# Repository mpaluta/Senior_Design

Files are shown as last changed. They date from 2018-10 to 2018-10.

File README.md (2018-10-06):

# Senior_Design

This repo hosts materials related to the design of "Flappy Bird", an endearingly-named RC airplane for our Notre Dame aerospace engineering senior design class. We designed, fabricated, and tested our airplane to perform to prescribed mission requirements.  

Our final report is located [here](/Box%20Files/Final%20Report/Final%20Report.pdf).

Takeoff and flight demo is located [here](Images/Takeoff_and_Flight.mov)

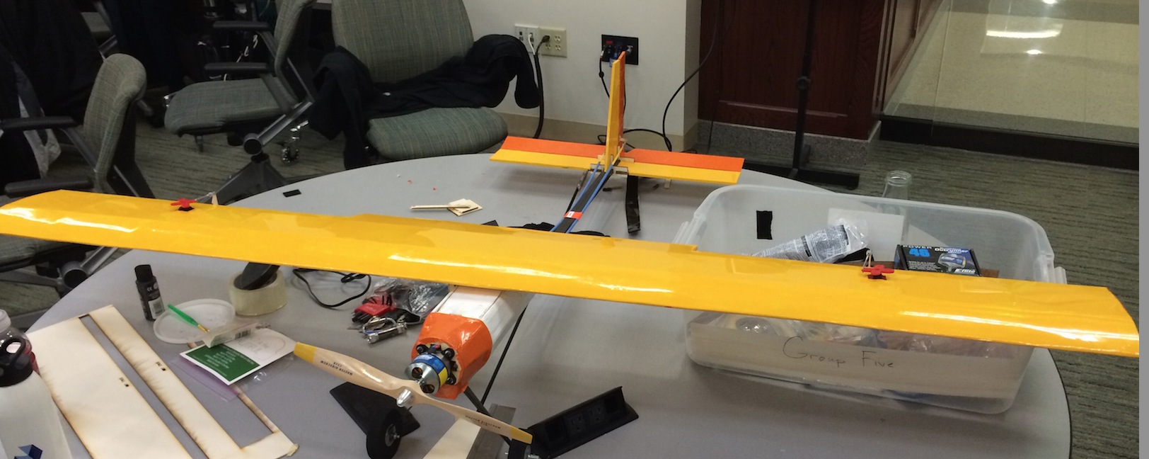
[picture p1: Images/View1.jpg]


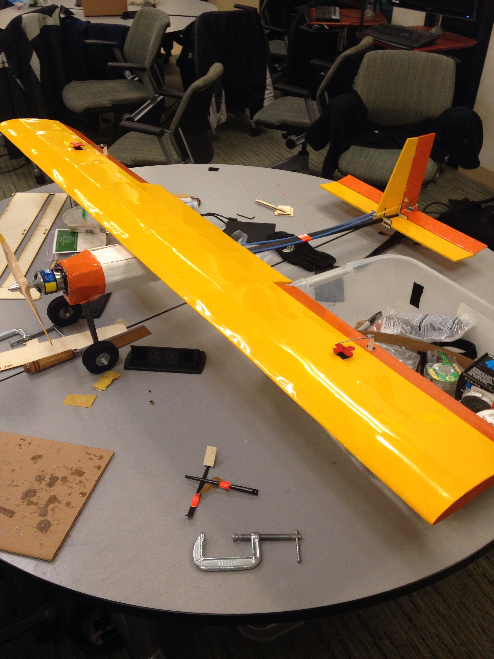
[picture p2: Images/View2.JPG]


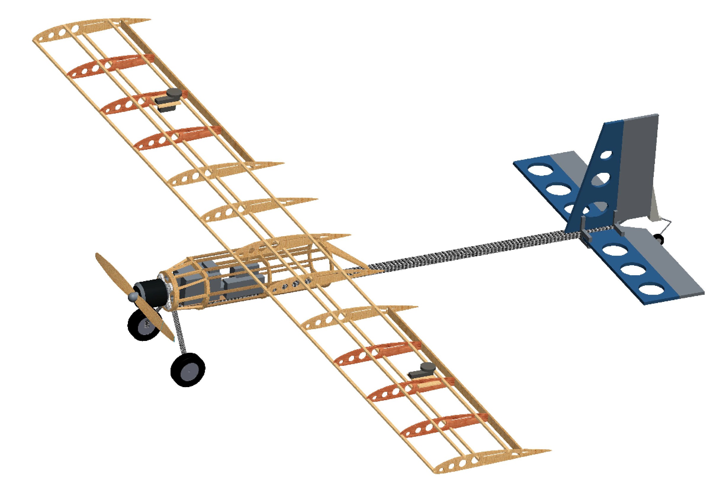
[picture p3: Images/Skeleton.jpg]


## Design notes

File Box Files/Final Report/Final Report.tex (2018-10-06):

\documentclass[titlepage]{article}
\usepackage{graphicx}
\usepackage{indentfirst}
\usepackage{array}
\usepackage{gensymb}
\usepackage{pdfpages}
\usepackage[bottom]{footmisc}
\usepackage[title,titletoc,toc]{appendix}
\renewcommand{\thetable}{\Roman{table}}
\renewcommand{\baselinestretch}{1.35}
\usepackage[margin=1in]{geometry}
\setlength{\parindent}{.4in}

\usepackage{fancyhdr} 
\pagestyle{fancy}
\lhead{\textsf{Design and Flight Analysis of the Remote-Controlled Flappy Bird Aircraft}}
\rhead{\textsf{\thepage}}
\cfoot{}
\renewcommand{\headrulewidth}{0.4pt}
\renewcommand{\footrulewidth}{0.4pt}

\begin{document}
\title{\textbf{Design and Flight Analysis of the Remote-Controlled Flappy Bird Aircraft}}
\author{Brian Quinn, Mark Paluta, Eliseo Miranda, Patrick Wall}
\date{May 9, 2014}
\maketitle

\begin{abstract}
Scale model, remotely-controlled aircraft are used extensively for hobby pilots, but also serve a secondary, educative purpose of allowing university students to apply aerodynamic theory to a physical flight application. In this design project, a high aspect ratio, low wing loading aircraft was designed to fly a mission in which it would be required to fly to high altitudes before performing an unpowered descent back to its cruising altitude. Implementing performance characteristics calculated using principles of fluid mechanics and aerodynamics, along with historical data from previous designs, the team of student engineers designed a minimalist vehicle, constructed from light woods and carbon fiber, that demonstrated speeds of up to 48 mph with climb rates as high as 1246 ft/min to meet the mission requirements, surpassing pre-flight predictions. Although flight data indicates that glide predictions far exceeded the observed values, the plane was able to successfully progress through each phase of the mission profile without issue and proved to be both maneuverable and well-controlled in the air, leaving the designers with confidence that subsequent design iterations would allow those performance issues to be resolved.
\end{abstract}

\tableofcontents
\addcontentsline{toc}{section}{List of Figures}
\addcontentsline{toc}{section}{List of Tables}
\listoffigures
\listoftables
\pagebreak

\section{Introduction}
For years, remotely-controlled aircraft have captured the interests of hobby enthusiasts of all ages and skillsets, combining ease of operation with a multitude of designs available as kits, templates, or ready-made models. For students at the university level, however, who have had exposure to flight principles like aerodynamics, dynamics, and fluid mechanics, scale aircraft provide a unique opportunity to translate that theory into a physical application at relatively low costs, allowing students to explore untested design concepts and construction ideas in an environment that celebrates challenges and mishaps as an opportunity to learn. 

It is this concept that inspired the 2014 senior design capstone project for which students were tasked with working cohesively as a team to construct viable aircraft, complete with useable control surfaces, guided by their knowledge of aerodynamics concept and the skills of seasoned pilots. Steered by a mission mandate requiring that each aircraft be designed to climb to as high an altitude as possible in ten seconds before performing an unpowered glide back down to the cruising altitude, the four students of DBC Industries, referred to herein as the Team, created an aircraft colloquially referred to as, ``The Flappy Bird", a minimalist airframe designed to climb quickly while also allowing the craft to glide for long periods of time. This report details the design and construction process of the final vehicle and also analyzes the results of preliminary flight testing, permitting a comparison of predicted vehicle maneuverability and the observed capabilities during flight.

\section{Mission Profile}
The mission profile for this design project, as alluded to previously, consists of three distinct phases of flight operation. In Phase I, the aircraft must take off under its own power and maintain low altitude, level flight while its stability and control are verified by the remote pilot. Pending a successful checkout, the aircraft then proceeds to Phase II in which it must begin to climb to as high an altitude as possible in a ten second interval. From there, Phase III begins with a short period of high altitude, level flight before the craft returns to its original altitude through an unpowered glide, with focus placed on the rate of descent of the aircraft. 

\section{Detailed Design}
\label{design}
Before construction began on the physical aircraft, an exhaustive design process was undertaken to ensure the mission requirements could be met during flight testing, guided by the designation of two primary design drivers. Of utmost concern was the aircraft's overall weight. Although the aircraft was required to carry data collection sensors and servo motors to drive the control surface deflections, the Team chose a minimalist approach to the design of the fixed structure. Unlike service aircraft which require a rigid, metal skin around the fuselage and wing surfaces, the conditions under which these scale aircraft flew exacted far less stress on the airframe, allowing large portions of the structure, that might otherwise be covered in wood sheeting, to be replaced with monokote, a plastic covering that bonds to materials when heated. As the CAD model in Figure \ref{noskin} shows, the elimination of rigid skin allowed the Team to use wood only where necessary to defined the shape of the airframe or to provide a surface onto which sensors and other payloads could rest.
\begin{figure}[h]

\caption{Isometric view of CAD model highlighting minimalist airframe structure}
\label{noskin}
\end{figure}
These material savings along with use of light woods such as balsa and spruce allowed the Team to construct a robust aircraft with a low structure weight, putting less stress on the motor during climb and requiring less of the wing during the descent glide.

To further address the issue of weight, a rectangular carbon fiber rod was chosen as the main structural element of the fuselage. As the backbone for both the fuselage and tail assemblies, the rod would take most of the stress on the airframe during flight, but would do so with minimal added weight. The fuselage was approximately cylindrical, tapering off in roughly a cone at the trailing edge and built up from the carbon fiber rod that ran through the length of its underbelly. It also housed most of the internal electronics with the exception of two aileron servos and a pitot tube in the main wing. Protruding from the front of the fuselage structure was a double-thick bulkhead upon which the motor and propeller assembly were affixed.

Located under the fuselage and epoxied directly to the front end of the carbon fiber rod, the main landing gear, experienced the most stress of any component on the aircraft due to its direct impact with the ground on landing attempts, and thus was attached strongest part of the aircraft allowing the gear system to transfer energy out of its legs upon impact. The connection points to the fuselage were also reinforced with a plywoord box, epoxied to the carbon fiber on both sides of the gear, to prevent any torquing motions from ripping the gear off of the aircraft. At the aft end of the aircraft, a small, steerable wheel was attached directly to the rudder, reducing the number of mechanical linkages and improving the takeoff performance due to the increase angle of attack of the wing while rolling on the ground. Attaching the wheel to the rudder negligibly reduced the ground control of the aircraft but improved weight characteristics, which was more desirable for the given mission profile.

The secondary driver employed in this design was a high lift-to-drag performance ratio. As outlined in the course textbook, a high lift force with a correspondingly low drag force promotes a lower descent rate during the gliding phase of flight, allowing the aircraft to remain aloft for proportionally longer periods of time. Although drag is a phenomena affecting all parts of the aircraft structure, the design of the main wing was of greatest concern to the Team as it has the largest overall effect on the ratio and, consequently, was the most challenging and, arguably, most important aspect of the design. 

Climb and glide are located at the opposite ends of the design spectrum when seeking an optimimum aspect ratio for a main wing. A small aspect ratio will help with climb and maneuverability while a large aspect ratio increases the performance during glide. To address each of these, an aspect ratio of 7 was selected to strike a mean between the two extremes, leading to a total wing span of 66 inches and a constant chord length of 9.6 inches. These design characteristics were implemented using a Clark Y flat-bottom airfoil. Used extensively in remote-controlled aircraft applications, the flat bottom afforeded the Team the ability to attach a mounting plate to the underside of the wing, allowing it to rigidly screw down onto the fuselage structure. The Clark Y also has the advantage of excellent lifting qualities at the low to middle range angles of attack at which the aircraft would be flying. A detailed drawing depicting the Clark Y shape and the rib structure of the aircraft can be found below in Figure \ref{wing} which also highlights the dimensions of the main wing structure.

\begin{figure}[h]
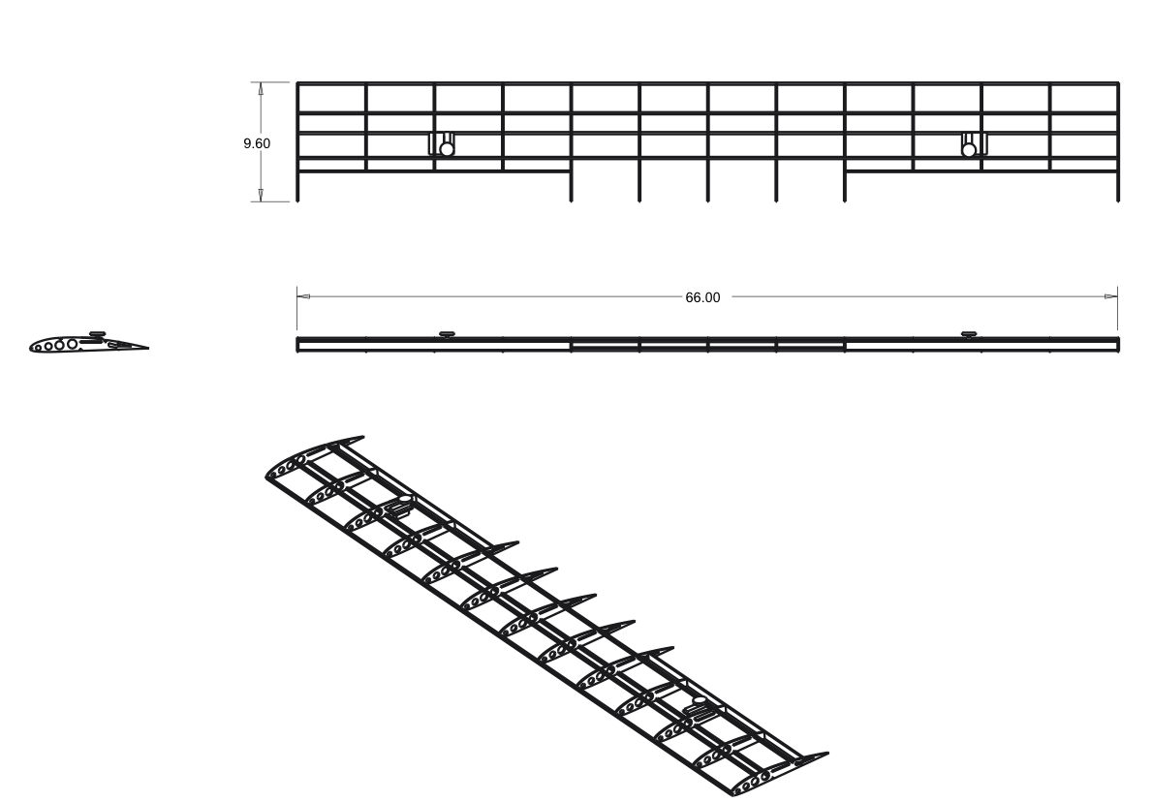
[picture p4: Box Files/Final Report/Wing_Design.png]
 
 \caption{Dimensioned model of the main wing depicting rib structure as well as airfoil shape and positioning.}
\label{wing}
\end{figure}

The tail was of conventional design placed at the free end of the carbon fiber rod protruding from the fuselage as seen in Figure \ref{noskin}. One of the main concerns of this design, however, was the potential for severe torquing from the lift forces generated by the tail surfaces. Addressing these issues early in the design process, the thickness of the carbon fiber rod was doubled, as was the thickness of the plywood used to construct the tail surfaces, leading to structurally sound design as seen in Figure \ref{tail} below, which also highlights the main dimensions, in inches, of the horizontal and vertical tail surfaces. A custom bracket was designed for the attachment of the tail surfaces to the carbon fiber, and each tail surface was anchored, using epoxy, to the bracket at two locations, thus preventing twisting. The elevator and rudder control surfaces were overdesigned to provide more than sufficient control of the aircraft and prevent flutter or twist in-flight. Although Figure \ref{tail} shows large holes in the tail surface, these were monokoted over in the final design, allowing weight savings without any detriment to performance.

\begin{figure}[h]
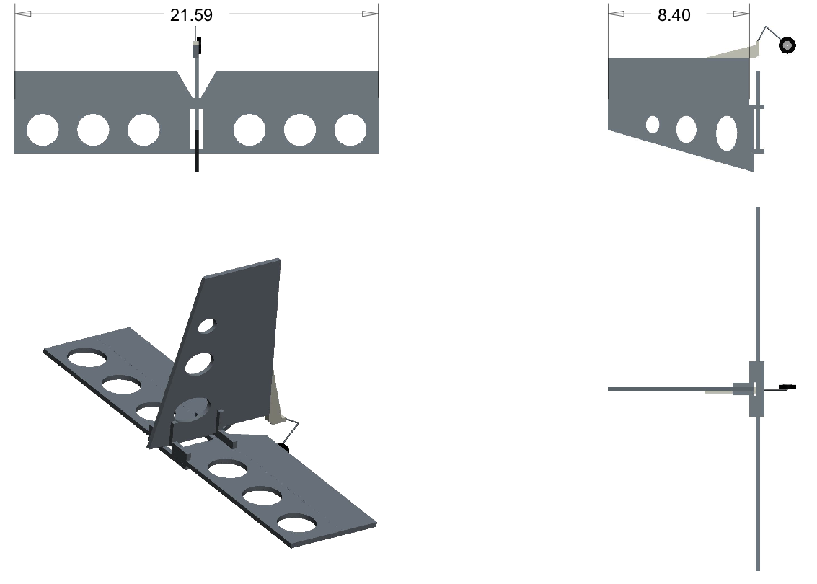
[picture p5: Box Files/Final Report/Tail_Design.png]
 
 \caption{Tail design detailing important dimensions and weight-saving structural designs.}
\label{tail}
\end{figure}
 
Rouding out the design, the aircraft used a 1.25 horsepower motor, capable of providing approximately 3.5 pounds-force of thrust. With a final takeoff weight of 5 pounds, including a 0.84 pound payload, this yielded a final thrust-to-weight ratio of 0.7. The motor powered a 13-inch propeller with an 8-inch pitch which created the power to move the craft through the air. As the main wing was bolted onto the fuselage before flight, hatches in both the top and side of the fuselage were used to allow access to internal components without removing the wing. The final flight vehicle is shown below in Figure \ref{real} in a picture taken just seconds after the final component of the fuselage was added, completing the craft.

Design characteristics of the aircraft were chosen using a Figure of Merit analysis, detailed and tabularized in Appendix A. The Figure of Merit analysis assigns numerical weights to different component designs based on drivers such as weight and size. The component with the most favorable weighting and ease of construction was the one chosen for use in the design.
\begin{figure}[h]
 
 \caption{Flappy Bird aircraft seconds after completion}
\label{real}
\end{figure}

\section{Predictions from Spreadsheet Analysis}
As part of the detailed design, a series of spreadsheets were used to determine relative values for vehicle handling qualities and component design. Perhaps one of the most integral factors for determining the aircraft's ability to perform well within the mission constraints is the wing loading as it plays a significant role in both an aircraft's climb and glide performance. As mentioned previously, glide performance is the mission phase in most need of optimization and, as such, the wing loading on the vehicle was determined based on performance during descent, for which a low wing loading is desired. Assuming a ground elevation of 823 feet in Bremen, Indiana, the town in which the field is located, the wing loading during glide was predicted to amount to approximately 13 oz/ft$^2$, a value corroborated by the pilots who would be controlling the aircraft during flight testing.

Given these flight characteristics and data culled from previous years' planes, the final climb rate of the aircraft was predicted to be 1,100 feet per minute, although the Team determined early on that the actual rate would decrease due to the structure weight of the high aspect ratio wing. Over the stated ten second time interval, this climb rate predicted a gain in altitude of approximately 200 feet. Assuming the unpowered glide would begin at this altitude, it was estimated that the aircraft would lose 152 feet of altitude every minute, thus requiring approximately 78 seconds to return to its original cruising altitude. As before, this glide rate assumes ideal flight conditions and is expected to diminish somewhat during flight testing. While at level flight, the design parameters in the spreadsheet predicted a cruising speed of 44 miles per hour.

Those spreadsheets that were used in the design process are attached at the back of this report as Appendix B. It should be noted that these were used merely as guides for ranges of acceptable values and, in many cases, actual design decisions were made based on input from both the pilots and teaching assistants who pulled design advice from previous experience.

\section{Flight Test Results}
During flight testing, the Flappy Bird flew a total of two test runs, each following the three phases of the mission profile. To numerically track the performance of the aircraft on these flights, altitude and speed data were collected by an onboard sensor package, including a pitot static tube mounted starboard wing tip. After eliminating the data collected while the plane was readied for flight, Figure \ref{Trial}, containing altitude data over each test flight, and Figure \ref{speed}, a graphic showing the speed of the aircraft during its flight testing, were produced to give a reader a visual representation of the information collected during flight testing.

\begin{figure}[h]
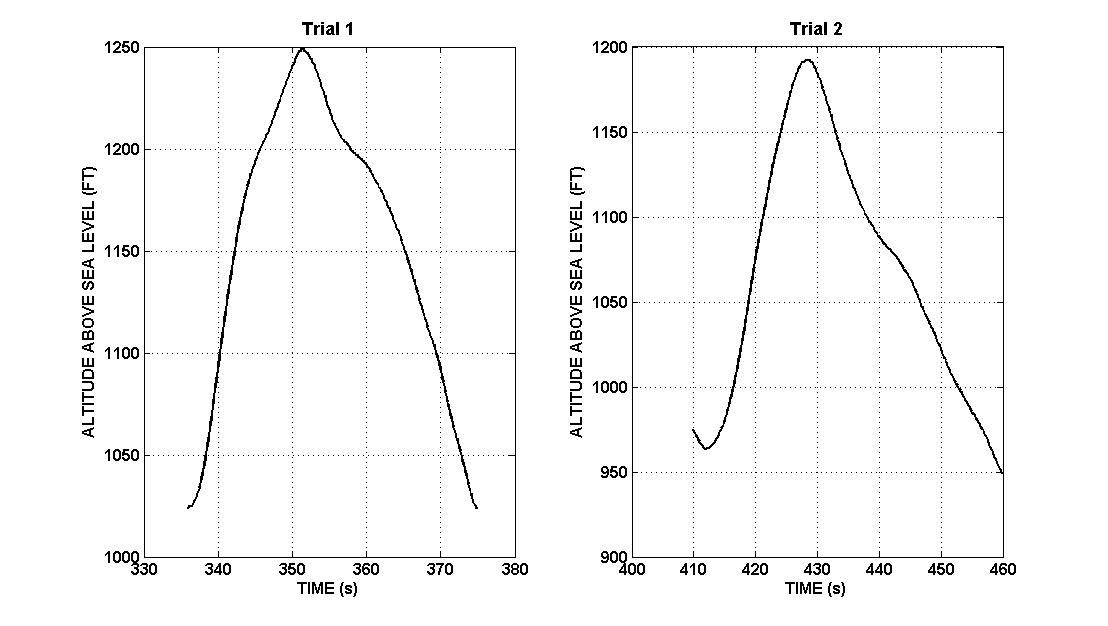
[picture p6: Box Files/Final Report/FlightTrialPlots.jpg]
 
 \caption{Climb and descent profiles flown by the Flappy Bird aircraft during two flight tests.}
\label{Trial}
\end{figure}

\begin{figure}[h]
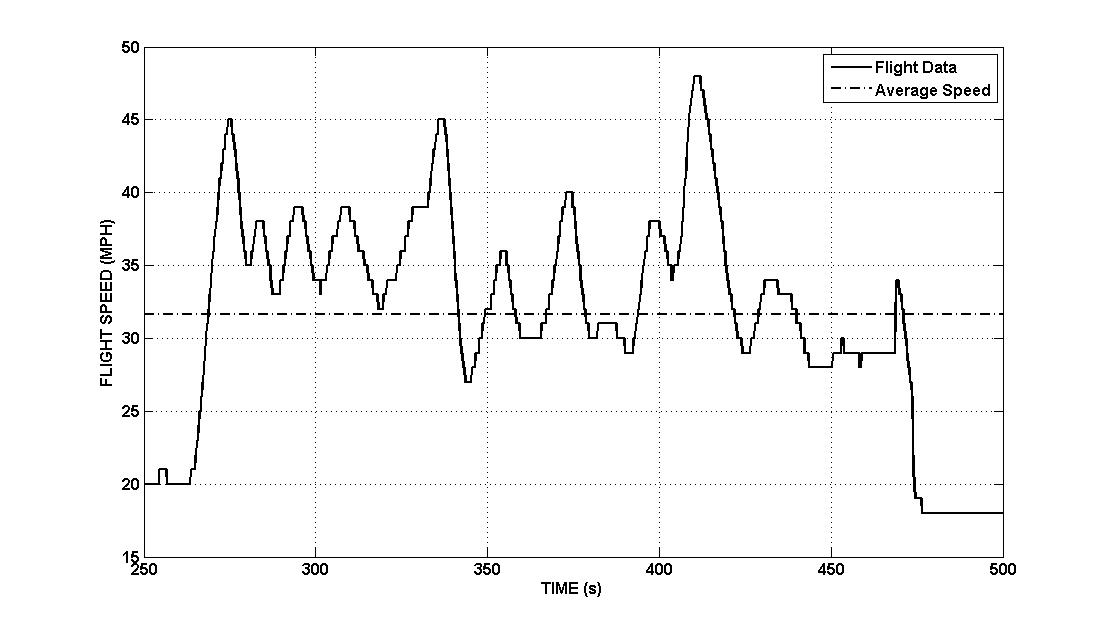
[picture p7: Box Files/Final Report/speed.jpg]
 
 \caption{Speed of Flappy Bird aircraft measured by onboard sensors throughout flight test.}
\label{speed}
\end{figure}

Focusing first on Figure \ref{Trial}, one can easily see that the climb and glide performance were similar through both test flights. In Trial 1, the aircraft was able to make a rapid ascent to an altitude of 1250 feet above sea level, or approximately 400 feet above the ground before gliding back to its original cruising altitude in a time interval of 24 seconds. In Trial 2, the pilots were able to make a more uniform climb up to the aircraft's peak altitude of 1900 feet above sea level before gliding back down to altitude in 26 seconds. 

Using this data, the Team was able to calculate rates for both ascent and descent for the two flight profiles. The maximum rate of climb for this aircraft, 1246 ft/min occured in the first leg of the ascent in Trial 1 as illustrated by the steep gradient from the cruising altitude to approximately 1200 ft. That ascent also saw the lowest rate of climb, 548 ft/min, during the final climb from 1200 feet to 1250 feet in altitude.

In a similar manner, the Team also conducted an analysis of descent, or glide, rates. As depicted clearly in the Trial 2 diagram of Figure \ref{Trial}, the final leg of descent, from approximately 1050 ft to the cruising altitude, represents the slowest measured rate of descent of the aircraft at 405 ft/minute. This was counteracted by a 596 ft/min descent rate between 1200 ft and the cruising altitude in Trial 1.

Each of the two trials depicted in Figure \ref{Trial} took place during a single, continuous test flight. Therefore, Figure \ref{speed}, upon which focus will now be placed, depicts the aircraft speed through both trials from first takeoff to final landing. As the horizontal dashed line indicates, the mean speed of the aircraft during its test flights was 31.6 mph, a number clearly affected by the low-speed regions of the figure surrounding takeoff and landing. During the flight, however, the aircraft also reached a peak speed of 48 mph, showing that speeds like the 44 mph predicted by the spreadsheet were, in fact, possible with this aircraft.  

Using this flight data the figure of merit for the flight testing, the success factor, was calculated using the formula presented in Equation \ref{success} as

\begin{equation}
S = (dH/dt)_c + (dH/dt)_g - \Delta(dH/dt)_c - \Delta(dH/dt)_g,
\label{success}
\end{equation} 
where $(dH/dt)$ represents the rate of climb or glide, identified by the subscripts ``c" and ``g", respectively, and $\Delta(dH/dt)$ represents the absolute difference between the predicted and actual rates of climb and glide following the same subscript identifications as before. After calculating each of these quantities, the flight success factor was determined to be 441.94 ft/min, approximately 47 \% of the success factor of 947.66 ft/min calculated assuming a perfect ascent and descent using the numbers produced by the design spreadsheets.

\section{Discussion}
For a first iteration of a design idea, the Flappy Bird performed admirably during its flight testing and proved an airworthy and highly maneuverable aircraft. As the success factor indicates, however, further iterations would require that work be done to improve its performance in a few key areas. As mentioned in Section \ref{design}, the two primary design drivers were geared towards optimizing the glide rate of the aircraft, an area in which the aircraft, admittedly, struggled. Its performance in this area, however, is well explained.

On the day of flight testing, strong winds were predicted and observed at the field during most of the flight test runs, this test proving no exception. Although these winds were within the acceptable limits of flying, they did have a deleterious effect on the rates of climb and glide due to their negative effects on the lifting surfaces. During ascent to the peak altitude, the pilots chose to climb at an angle of attack lower than might have normally been pursued to prevent the wind from causing a nose up moment that might stall the wing. Therefore, the rates shown in Figure \ref{Trial} may not necessarily be representative of the full capabilities of the aircraft. Similarly for glide, although the pilots attempted to fly into the wind to gain favorable lift performance, strong updrafts continued to push the wing towards stall, necessitating that they enter onto a steeper glide slope than might otherwise have been possible. The pilots, however, push the plane to the best acceptable limits during their flight so the data presented, although possibly skewed by the wind, represents the aircraft's best performance in adverse conditions.

The weather is not the sole focus of analysis for the aircraft as improvements could also be made in the design itself. If one recalls, aircraft weight was the primary design driver for the Flappy Bird aircraft, a decision that ultimately led to the minimalist design flown on the flight day. During the conceptualization process, this arrangement was predicted to fare well in both climb and glide, allowing the Team to strike a balance between climb and glide performance. If one recalls the mission profile, a fast climb, gained by a high thrust-to-weight ratio, would permit the Flappy Bird to reach a substantial altitude at the end of 10 seconds, permitting a longer glide time by increase the distance through which the aircraft would have to glide to level off back at its cruising altitude. The weight, coupled with the high aspect ratio, low wing loading main wing would also help to improve the glide performance by increasing the lift on the main wing through the entirety of the gliding phase. When physically constructed, however, the small fuselage and its limited exterior surface area, created a design challenge for the Team to place the main wing and components such that the aircraft remained stable during flight and maintained an acceptable margin between the center of lift on the main wing and the center of gravity of the aircraft as a whole. Through creative use of the wall and floor surfaces, this margin was obtained, but it provided only a small travel between stable and unstable, possibly creating more issues for the pilots during flight.

Despite the design and performance issues, most of which were anticipated, the aircraft did manage to yield a large success factor. As Equation \ref{success} indicates, the success factor is determined by both climb and glide rates. Previous senior design aircraft appeared to all perform climbs at rates approaching 1100 ft/min and, given the Team's design for the Flappy Bird, rates in the top end of the historical data were thought to correspond better with the performance characteristics that the aircraft catered to. As the flight test data indicates, not only was the aircraft capable of reaching that 1100 ft/min speed, but was actually able to climb at a rate significantly faster than that predicted even despite the strong winds. Although this climb rate was not maintained throughout the ten second interval, it allowed the aircraft to reach an altitude of 1250 ft above sea level, placing it in an advantageous position to begin its glide. As mentioned previously, there were many factors that contributed to a lower average climb rate throughout the two test flights, but the Team believes it can deem the flight a success because the aircraft surpassed the original predictions which were made assuming perfect flight conditions.

Although the success in glide was not as pronounced as that in climb, the Team still believes that the results are not as unexpected as one might first believe. The spreadsheet analysis, again, conducted assuming perfect, calm flight conditions, placed the Flappy Bird's minimum descent rate at 152 feet of altitude lost for every minute of flight, a value which was over three times less than the minimum descent rate of 405 ft/min observed on flight day. The team did not, however, expect to reach this low glide value simply because of the imperfection of the design. When assuming a perfect wing section in the spreadsheets, wind is assumed to flow over the airfoil surface without any perturbations or abberations, leaving a smooth boundary layer and a consistent lift on the airfoil. Although the smooth surface was achieved using monokote over the wing, possible imperfections in the both the airfoil design and its attachment scheme to the fuselage assuredly led to a fractional loss in lift not able to be reproduced on spreadsheets which did not take into account any of the finer design details of the aircraft, leading to the lower-than-predicted results. Regardless of this fact, the Team stresses that, for a basic first design, the flight testing went extremely well, leaving the aircraft with 47 \% of its intended success design and only falling short in areas for which the imperfections are well-explained and well understood. 

\section{Conclusion}
When any new vehicle of component design begins to take shape at any aerospace company, every detail is meticulously analyzed using both computational and physical test methods to ensure the final product is safe for customers and reliable for its stated design mission. Although scale model aircraft, such as those used in this project, do not fall under such stringent requirements, the need to verify design is key in both situations. The Flappy Bird aircraft was very much a conceptual design turned physical model flown for the purposes of demonstrating basic knowledge of flight principles and aerodynamic theory and, by all accounts, the aircraft succeeded in its purpose. Not only was the vehicle able to successfully takeoff and land under its own power, but during flight was proven to be highly maneuverable and exceeded expections in climb performance. For a first design iteration, however, the losses observed in glide were acceptable and easily addressed in subsequent design were there to be more. 

The benefit of remote-controlled aircraft is the minimal price paid for possible performance issues. Whereas commercial aircraft components may cost thousands of dollars to test and validate, the kits used in this project cost a minuscule fraction of that, promoting daring designs and welcoming issues as an opportunity to learn. Therefore, although the flight data was not always as predicted, it provided the impetus to return to the conceptual design of the aircraft to identify areas in which the physical structure and performance characteristics of the aircraft could be improved if the vehicle were to be redesigned. The most important takeaway, however, is that the aerospace education gained thus far has allowed the Team to construct a vehicle capable of flight and capable of meeting a specific mission profile with tools taught in the classroom, providing motivation to seek out design opportunities in the commerical industry but also providing confidence to the engineers that their education is applicable to real-world design problems and their experience is broad enough to enable them to address and solve problems that may occur throughout the process.

\newpage

\begin{appendices}
\section{Figure of Merit Analysis}
Although this design is ultimately constrained by the requirements of the mission statement, a determination of favorable attributes for an aircraft of this type was conducted using a figure of merit (FoM) analysis. An FoM analysis is part of a design approach that is used to select components that form an aircraft's structure in an efficient and objective manner. Although the analysis cannot produce design dimensions, it can provide a numerical point of comparison between different variations of airframe components under consideration. As Table \ref{tab:FoMGen} shows, physical and performance characteristics are evaluated across a rating system between 1 and 5, with larger numbers representing a greater importance to the design drivers. The row totals are then summed and each characteristic is assigned a bias percentage which determines its overall priority in the final design. 

\begin{table}[h!]
\caption{Figures of Merit for Aircraft Performance}
\resizebox{\textwidth}{!}{%
\begin{tabular}{|c|c|c|c|c|c|c|c|c|}
\hline
 & \textbf{Weight} & \textbf{High L/D} & \textbf{Size} & \textbf{Ease of Construction} & \textbf{Stability \& Control} & \textbf{Payload} & \textbf{Row Totals} & \textbf{Bias} \\
\hline
\textbf{Weight} & 0.00 & 4.00 & 4.00 & 4.00 & 4.00 & 5.00 & 21.00 & 23 \% \\
\hline
\textbf{High L/D} & 2.00 & 0.00 & 4.00 & 4.00 & 3.00 & 5.00 & 18.00 & 20 \% \\
\hline
\textbf{Size} & 2.00 & 2.00 & 0.00 & 2.00 & 2.00 & 2.00 & 10.00 & 11 \% \\
\hline
\textbf{Ease of Construction} & 2.00 & 2.00 & 4.00 & 0.00 & 1.00 & 3.00 & 12.00 & 13 \% \\
\hline
\textbf{Stability \& Control} & 3.00 & 3.00 & 4.00 & 5.00 & 0.00 & 4.00 & 19.00 & 21 \% \\
\hline
\textbf{Payload} & 1.00 & 1.00 & 4.00 & 3.00 & 2.00 & 0.00 & 11.00 & 12 \% \\
\hline
\end{tabular}}
\label{tab:FoMGen}
\end{table}

Once the design biases have been set, the figure of merit analysis is conducted on each of the possible component configurations considered for the final design. Table \ref{tab:wing} illustrates the process for the main wing selection. Unlike Table \ref{tab:FoMGen}, component analyses ratings are based on each configuration's benefit or detriment to the stated design drivers, with larger numbers representing more beneficial performance. These rankings are based on research into each possible configuration with special care taken to identify the strengths and weaknesses of each design. To finally determine the most appropriate component variation for the mission profile, a weighted average of the figures of merit for each configuration was tabulated, appearing on the bottom row of the matrix. Matrices for each of the other component analyses are located in Tables \ref{tab:control}-\ref{tab:motor}.

\begin{table}[h!]
\caption{Wing Design Matrix}
\resizebox{\textwidth}{!}{%
\begin{tabular}{|c|c|c|c|c|c|c|}
\hline
& \textbf{Monoplane} & \textbf{Biplane} & \textbf{Tandem Wing/Canard} & \textbf{Flying Wing/Blended Body} & \textbf{Winglets} & \textbf{Bias} \\
\hline
\textbf{Weight} & 4.00 & 3.00 & 3.00 & 5.00 & 5.00 & 23 \% \\
\hline
\textbf{High L/D} & 3.00 & 4.00 & 3.00 & 3.50 & 2.00 & 20 \% \\
\hline
\textbf{Size} & 3.00 & 1.00 & 3.00 & 4.00 & 5.00 & 11 \% \\
\hline
\textbf{Ease of Construction} & 5.00 & 2.00 & 2.00 & 1.00 & 5.00 & 13 \% \\
\hline
\textbf{Stability \& Control} & 4.50 & 3.00 & 2.00 & 1.00 & 1.00 & 21 \% \\
\hline
\textbf{Payload} & 3.00 & 3.00 & 3.00 & 1.50 & 3.00 & 12 \% \\
\hline
\textbf{Column Average} & \textbf{\underline{3.81}} & \textbf{2.85} & \textbf{2.66} & \textbf{2.81} & \textbf{3.33} & \\
\hline
\end{tabular}}
\label{tab:wing}
\end{table}

The results of each analysis were not entirely unexpected given the common history of these types of aircraft. Table \ref{tab:wing} shows that the single wing is the most advantageous wing configuration because of its low weight and relative ease of construction. Beyond those, it also boasts a high level of stability and average scores in all of the remaining categories, highlighting it as the best possible configuration.

Scoring highly in the same categories as the wing, the conventional tail also logged a markedly higher score than its competitors. Historical data comparisons show that the conventional tail has the lowest weight of the three variations in the category and, due to its right angle mounted design, scores well for ease of construction as well.

The final component selection of note is that of the landing gear. Historically, the three wheel trike configuration has a heavier under-mount system than other options such as the skids and tail gear which would suggest that it would conflict with the primary design driver of weight. In this instance, however, the additional stability gained over other gear options provided enough justification to the team to prioritize stability over weight. In addition to stability advantages, the trike gear also provides the aircraft with a more forgiving structure on which to land and takeoff. The three wheel configuration elevates the underbelly off the ground and provides some level of shock absorption during landing, preventing damage to the fuselage or lifting surfaces. 

\begin{table} [h!]
\caption{Control Surface Component Matrix}
\resizebox{\textwidth}{!}{%
\begin{tabular}{|c|c|c|c|c|c|}
\hline
& \textbf{2 Ailerons, 2 Elevators, 2 Flaps} & \textbf{2 Ailerons, 1 Elevator, 2 Flaps} & \textbf{2 Ailerons, 2 Elevators} & \textbf{Two Elevons} & \textbf{Bias} \\
\hline
\textbf{Weight} & 1.00 & 2.00 & 3.00 & 5.00 & 23 \%\\
\hline
\textbf{High L/D} & 5.00 & 4.00 & 3.00 & 1.00 & 20 \% \\
\hline
\textbf{Size} & 1.00 & 2.00 & 3.00 & 5.00 & 11 \% \\
\hline
\textbf{Ease of Construction} & 1.00 & 1.00 & 3.00 & 5.00 & 13 \% \\
\hline
\textbf{Stability \& Control} & 2.00 & 2.00 & 4.00 & 1.00 & 21 \% \\
\hline
\textbf{Payload} & 0.00 & 0.00 & 0.00 & 0.00 & 12 \% \\
\hline
\textbf{Column Average} & \textbf{1.88} & \textbf{2.02} & \textbf{\underline{2.85}} & \textbf{2.77} & \\
\hline
\end{tabular}}
\label{tab:control}
\end{table}

\begin{table}[h!]
\caption{Landing Gear Component Matrix}
\resizebox{\textwidth}{!}{%
\begin{tabular}{|c|c|c|c|c|c|c|c|}
\hline
& \textbf{None} & \textbf{Trike} & \textbf{Skids} & \textbf{Retractable} & \textbf{Tail} & \textbf{Monowheel} & \textbf{Bias} \\
\hline
\textbf{Weight} & 5.00 & 3.00 & 4.00 & 1.00 & 3.50 & 4.00 & 23 \%\\
\hline
\textbf{High L/D} & 5.00 & 3.00 & 4.00 & 1.00 & 4.00 & 4.00 & 20 \%\\
\hline
\textbf{Size} & 5.00 & 3.00 & 3.00 & 1.00 & 3.50 & 4.00 & 11 \% \\
\hline
\textbf{Ease of Construction} & 3.00 & 5.00 & 3.00 & 1.00 & 4.00 & 2.00 & 13 \% \\
\hline
\textbf{Stability \& Control} & 0.00 & 5.00 & 1.00 & 3.00 & 2.00 & 1.00 & 21 \% \\
\hline
\textbf{Payload} & 0.00 & 0.00 & 0.00 & 0.00 & 0.00 & 0.00 & 12 \% \\
\hline
\textbf{Column Average} & \textbf{3.09} & \textbf{\underline{3.32}} & \textbf{2.65} & \textbf{1.30} & \textbf{2.93} & \textbf{2.63} & \\
\hline
\end{tabular}}
\label{tab:gear}
\end{table}

\newpage 

\begin{table}[h!]
\caption{Tail Configuration Matrix}
\centering
\begin{tabular}{|c|c|c|c|c|}
\hline
& \textbf{Conventional} & \textbf{V-Tail} & \textbf{H-Tail} & \textbf{Bias}\\
\hline
\textbf{Weight} & 4.00 & 4.00 & 2.00 & 23 \%\\
\hline
\textbf{High L/D} & 5.00 & 5.00 & 2.00 & 20\%\\
\hline
\textbf{Size} & 3.00 & 3.00 & 2.00 & 11 \% \\
\hline
\textbf{Ease of Construction} & 5.00 & 2.00 & 5.00 & 13 \% \\
\hline
\textbf{Stability \& Control} & 4.00 & 2.00 & 5.00 & 21 \% \\
\hline
\textbf{Payload} & 3.00 & 3.00 & 3.00 & 12 \% \\
\hline
\textbf{Column Average} & \textbf{\underline{4.10}} & \textbf{3.29} & \textbf{3.14} & \\
\hline
\end{tabular}
\label{tab:tail}
\end{table}

\begin{table}[h!]
\caption{Motor Configuration Matrix}
\centering
\begin{tabular}{|c|c|c|c|}
\hline
& \textbf{Mono-Tractor} & \textbf{Mono-Pusher} & \textbf{Bias}\\
\hline
\textbf{Weight} & 4.00 & 4.00 & 23 \%\\
\hline
\textbf{High L/D} & 4.00 & 2.00 & 20 \%\\
\hline
\textbf{Size} & 3.00 & 3.00 & 11 \% \\
\hline
\textbf{Ease of Construction} & 5.00 & 3.00 & 13 \% \\
\hline
\textbf{Stability \& Control} & 4.00 & 2.00 & 21 \% \\
\hline
\textbf{Payload} & 3.00 & 3.00 & 12 \% \\
\hline
\textbf{Column Average} & \textbf{\underline{3.90}} & \textbf{2.82}& \\
\hline
\end{tabular}
\label{tab:motor}
\end{table}
\newpage

\section{Design Guidance Spreadsheets}
\begin{minipage}{\textwidth}
\includepdf[scale=0.9]{SpreadsheetsIterTow.pdf}
\end{minipage}
\includepdf[pages={1}]{SpreadsheetsWingLD.pdf}
\includepdf[pages={1}]{SpreadsheetsWing.pdf}
\includepdf[pages={-}]{SpreadsheetsTail.pdf}
\includepdf[pages={1}]{Skin.pdf}
\end{appendices}
\end{document}

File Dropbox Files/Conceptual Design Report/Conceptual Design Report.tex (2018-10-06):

\documentclass[titlepage]{article}
\usepackage{graphicx}
\usepackage{indentfirst}
\usepackage{array}
\usepackage{gensymb}
\usepackage[bottom]{footmisc}
\usepackage[title,titletoc,toc]{appendix}
\renewcommand{\thetable}{\Roman{table}}
\renewcommand{\baselinestretch}{1.75}
\setlength{\textheight}{9in}
\setlength{\textwidth}{6.75in}
\setlength{\headheight}{0in}
\setlength{\headsep}{0in}
\setlength{\topmargin}{0in}
\setlength{\oddsidemargin}{0in}
\setlength{\evensidemargin}{0in}
\setlength{\parindent}{.4in}

\begin{document}
\title{\textbf{Conceptual Design Report}}
\author{Brian Quinn, Mark Paluta, Eliseo Miranda, Patrick Wall}
\maketitle

\section{Introduction}
For many years, remotely-controlled aircraft have occupied the interest of hobby enthusiasts due to their compact form and flexibility in design. For university students, however, they also offer a lower-cost approach to physical applications of aerodynamic theories and principles that can be used to supplement lecture topics. In this iteration, the remote-controlled aircraft will be constructed based on information gathered from both historical models and governing equations, tasking senior level students with the goal of designing an entire flying structure capable of successfully undertaking a stated mission profile. The first step, and topic of this report, is the conceptual design of the airplane including the primary design drivers which determine the path of construction, and the physical design features that will enable the aircraft to fly its mission. It is during the conceptual design stage that the aircraft takes it preliminary form and baseline data are obtained to better guide construction towards an efficient and successful remote-controlled vehicle.

\section{Mission and Design Proposal}
The stated mission for this design project consists of three phases of aircraft flight operation. The aircraft must first take off, solely under its own power, and maintain low altitude, level flight. From there, it must begin to climb as fast and as high as it can over a ten second interval and level off at the top of its ascent. After circling at the new altitude and verifying its stability, the aircraft will perform an unpowered glide back to its original altitude, with the area of focus centered on the rate of descent during that glide.  

The primary design driver for this mission profile is aircraft weight. Although certain sensor packages and servo motors will necessarily be incorporated into the final design, weight savings can be gained from efficient design of the wing and fuselage structures to eliminate excess material weight. A low weight will help with both of the main objectives of the mission, climb and glide. For climb, a low-weight structure will not tax the fixed-thrust propeller motor as much as a heavier aircraft would on vertical ascent. On the gliding descent as well, a lighter aircraft should experience a more favorable descent gradient than heavier variants using the same lifting surfaces.

The secondary design driver is a high lift-to-drag (L/D) ratio. High performance in this area will promote a low descent rate during the gliding phase of flight, allowing the aircraft to remain aloft for an extended period of time. In this design, the glide performance was deemed the mission phase in most need of optimization and, as such, the choice of the two primary design drivers centers around the aircraft performance characteristics that will lead to the best glide performance.

There are a few key physical features on the proposed aircraft that will serve as main drivers towards the desired mission objectives. The main wing will have an aspect ratio of 7, leading to a total wingspan of 5 feet, 6 inches. The high aspect ratio will contribute to a low wing loading during descent which is favorable for glide performance. The wing will be mounted high on the fuselage to afford the aircraft increased roll stability during flight. 

Climb performance of the aircraft is determined not only by the aircraft design, but also that of its motor. This iteration will employ a 1.25 horsepower motor, capable of providing approximately 3 pounds-force of thrust. This motor will power a 13 inch propeller with an 8 degree pitch, a more than capable thrust allotment to provide the needed forward force to fly the aircraft. 

\section{Figure of Merit Analysis}
Although this design is ultimately constrained by the requirements of the mission statement, a determination of favorable attributes for an aircraft of this type was conducted using a figure of merit (FoM) analysis. An FoM analysis is part of a design approach that is used to select components that form an aircraft's structure in an efficient and objective manner. Although the analysis cannot produce design dimensions, it can provide a numerical point of comparison between different variations of airframe components under consideration. As Table \ref{tab:FoMGen} shows, physical and performance characteristics are evaluated across a rating system between 1 and 5, with larger numbers representing a greater importance to the design drivers. The row totals are then summed and each characteristic is assigned a bias percentage which determines its overall priority in the final design. 

\begin{table}[h!]
\caption{Figures of Merit for Aircraft Performance}
\resizebox{\textwidth}{!}{%
\begin{tabular}{|c|c|c|c|c|c|c|c|c|}
\hline
 & \textbf{Weight} & \textbf{High L/D} & \textbf{Size} & \textbf{Ease of Construction} & \textbf{Stability \& Control} & \textbf{Payload} & \textbf{Row Totals} & \textbf{Bias} \\
\hline
\textbf{Weight} & 0.00 & 4.00 & 4.00 & 4.00 & 4.00 & 5.00 & 21.00 & 23 \% \\
\hline
\textbf{High L/D} & 2.00 & 0.00 & 4.00 & 4.00 & 3.00 & 5.00 & 18.00 & 20 \% \\
\hline
\textbf{Size} & 2.00 & 2.00 & 0.00 & 2.00 & 2.00 & 2.00 & 10.00 & 11 \% \\
\hline
\textbf{Ease of Construction} & 2.00 & 2.00 & 4.00 & 0.00 & 1.00 & 3.00 & 12.00 & 13 \% \\
\hline
\textbf{Stability \& Control} & 3.00 & 3.00 & 4.00 & 5.00 & 0.00 & 4.00 & 19.00 & 21 \% \\
\hline
\textbf{Payload} & 1.00 & 1.00 & 4.00 & 3.00 & 2.00 & 0.00 & 11.00 & 12 \% \\
\hline
\end{tabular}}
\label{tab:FoMGen}
\end{table}

Once the design biases have been set, the figure of merit analysis is conducted on each of the possible component configurations considered for the final design. Table \ref{tab:wing} illustrates the process for the main wing selection. Unlike Table \ref{tab:FoMGen}, component analyses ratings are based on each configuration's benefit or detriment to the stated design drivers, with larger numbers representing more beneficial performance. These rankings are based on research into each possible configuration with special care taken to identify the strengths and weaknesses of each design. To finally determine the most appropriate component variation for the mission profile, a weighted average of the figures of merit for each configuration was tabulated, appearing on the bottom row of the matrix. Matrices for each of the other component analyses are located in Appendices \ref{sec:control}-\ref{sec:motor}

\begin{table}[h!]
\caption{Wing Design Matrix}
\resizebox{\textwidth}{!}{%
\begin{tabular}{|c|c|c|c|c|c|c|}
\hline
& \textbf{Monoplane} & \textbf{Biplane} & \textbf{Tandem Wing/Canard} & \textbf{Flying Wing/Blended Body} & \textbf{Winglets} & \textbf{Bias} \\
\hline
\textbf{Weight} & 4.00 & 3.00 & 3.00 & 5.00 & 5.00 & 23 \% \\
\hline
\textbf{High L/D} & 3.00 & 4.00 & 3.00 & 3.50 & 2.00 & 20 \% \\
\hline
\textbf{Size} & 3.00 & 1.00 & 3.00 & 4.00 & 5.00 & 11 \% \\
\hline
\textbf{Ease of Construction} & 5.00 & 2.00 & 2.00 & 1.00 & 5.00 & 13 \% \\
\hline
\textbf{Stability \& Control} & 4.50 & 3.00 & 2.00 & 1.00 & 1.00 & 21 \% \\
\hline
\textbf{Payload} & 3.00 & 3.00 & 3.00 & 1.50 & 3.00 & 12 \% \\
\hline
\textbf{Column Average} & \textbf{\underline{3.81}} & \textbf{2.85} & \textbf{2.66} & \textbf{2.81} & \textbf{3.33} & \\
\hline
\end{tabular}}
\label{tab:wing}
\end{table}

The results of each analysis were not entirely unexpected given the common history of these types of aircraft. Table \ref{tab:wing} shows that the single wing is the most advantageous wing configuration because of its low weight and relative ease of construction. Beyond those, it also boasts a high level of stability and average scores in all of the remaining categories, highlighting it as the best possible configuration.

Scoring highly in the same categories as the wing, the conventional tail also logged a markedly higher score than its competitors. Historical data comparisons show that the conventional tail has the lowest weight of the three variations in the category and, due to its right angle mounted design, scores well for ease of construction as well.

The final component selection of note is that of the landing gear. Historically, the three wheel trike configuration has a heavier under-mount system than other options such as the skids and tail gear which would suggest that it would conflict with the primary design driver of weight. In this instance, however, the additional stability gained over other gear options provided enough justification to the team to prioritize stability over weight. In addition to stability advantages, the trike gear also provides the aircraft with a more forgiving structure on which to land and takeoff. The three wheel configuration elevates the underbelly off the ground and provides some level of shock absorption during landing, preventing damage to the fuselage or lifting surfaces. 

\section{Predictions from Spreadsheet Analysis}
In addition to the figure of merit analysis, the provided aircraft design spreadsheets were used to determine finite numerical dimensions for each of the airframe components as well as providing some insight into the forces acting on the vehicle during flight. 

Our empty weight is expected to be around 1.5 pounds, leading to an estimated takeoff weight of approximately 3.7 pounds which is a typical weight based on previous senior design aircraft. This figured is based on a preliminary weight estimate consisting of 2 pounds of aircraft control and monitoring equipment and a vehicle structure factor of 0.4.

Perhaps one of the most important factors for determining the aircraft's ability to perform well within the mission constraints is the wing loading as it is an integral factor in the aircraft's climb and glide performance. As mentioned previously, glide performance is the mission phase in most need of optimization and, as such, the wing loading on the vehicle was determined based on performance during descent, during which a low wing loading is desired. True to form, assuming a glide from 1,400 ft ,assuming a ground elevation of 729 feet in South Bend, the wing loading during glide would only amount to about 0.81 lb/ft$^2$, or approximately 13 oz/ft$^2$, a wing loading that will surely help contribute to satisfactory glide performance.

Given these flight characteristics and data culled from previous design planes, the final climb rate of the aircraft was given a best-estimate of 1,100 feet per minute although that number is expected to decrease in flight testing due to the structure weight of the high aspect ratio wing. Over the stated ten second time interval, this climb rate allows a gain in altitude of approximately 200 feet. Assuming the unpowered glide will begin at this altitude, it is estimated that the aircraft will lose 2.5 feet of altitude every second and take approximately 73 seconds to return to its original cruising altitude. As before, this glide rate assumes ideal flight conditions and is expected to diminish somewhat during flight testing.
At the moment, the vehicle exhibits a lift-to-drag ratio of approximately 26 which falls within the average value for light cruise aircraft. Over the design and construction process, however, various drag reduction methods will be explored to increase this value. Control for the aircraft will be accomplished using two outboard ailerons, a rudder placed on the vertical tail, and a single elevator that occupies the entire trailing span of the horizontal tail plane. Once properly sized, these elements should provide sufficient control for the vehicle in flight.

Each spreadsheet used in this analysis is attached at the back of this report in the order of completion. Due to the constraints and requirements of this remote controlled aircraft, the engine and flap spreadsheets have been omitted. Please note the following as well: The takeoff and landing spreadsheet is not representative of the values expected during either phase of flight and quantities cited in both the refined weight and stability analyses are rough estimates and will be updated throughout construction with actual values. 

\section{Summary}

This aircraft is designed for all-around performance within the mission specifications with a strong emphasis on optimizing the glide performance of the vehicle. As mentioned previously, this will be accomplished by reducing the overall structure weight of the aircraft and achieving a high lift-to-drag ratio. The current design features a minimalist, cylindrical, tapered fuselage which will allow storage of the required payload instruments and sensors while streamlining the exposed surface. Taking lead from this design, the rest of the aircraft will employ only the materials necessary to ensure a robust and stable flight system. In addition to this simplistic design, the craft will employ a high aspect ratio wing that will help to optimize and prolong the time spent in glide without destroying the climbing ability of the aircraft. Overall, the team feels that this design will succeed where previous designs have failed and will provide exceptional performance during its flights.

\newpage

\begin{appendices}
\section{Control Surface Component Matrix}
\label{sec:control}
\begin{table} [h!]
\resizebox{\textwidth}{!}{%
\begin{tabular}{|c|c|c|c|c|c|}
\hline
& \textbf{2 Ailerons, 2 Elevators, 2 Flaps} & \textbf{2 Ailerons, 1 Elevator, 2 Flaps} & \textbf{2 Ailerons, 2 Elevators} & \textbf{Two Elevons} & \textbf{Bias} \\
\hline
\textbf{Weight} & 1.00 & 2.00 & 3.00 & 5.00 & 23 \%\\
\hline
\textbf{High L/D} & 5.00 & 4.00 & 3.00 & 1.00 & 20 \% \\
\hline
\textbf{Size} & 1.00 & 2.00 & 3.00 & 5.00 & 11 \% \\
\hline
\textbf{Ease of Construction} & 1.00 & 1.00 & 3.00 & 5.00 & 13 \% \\
\hline
\textbf{Stability \& Control} & 2.00 & 2.00 & 4.00 & 1.00 & 21 \% \\
\hline
\textbf{Payload} & 0.00 & 0.00 & 0.00 & 0.00 & 12 \% \\
\hline
\textbf{Column Average} & \textbf{1.88} & \textbf{2.02} & \textbf{\underline{2.85}} & \textbf{2.77} & \\
\hline
\end{tabular}}
\label{tab:control}
\end{table}

\section{Landing Gear Component Matrix}
\label{sec:gear}
\begin{table}[h!]
\resizebox{\textwidth}{!}{%
\begin{tabular}{|c|c|c|c|c|c|c|c|}
\hline
& \textbf{None} & \textbf{Trike} & \textbf{Skids} & \textbf{Retractable} & \textbf{Tail} & \textbf{Monowheel} & \textbf{Bias} \\
\hline
\textbf{Weight} & 5.00 & 3.00 & 4.00 & 1.00 & 3.50 & 4.00 & 23 \%\\
\hline
\textbf{High L/D} & 5.00 & 3.00 & 4.00 & 1.00 & 4.00 & 4.00 & 20 \%\\
\hline
\textbf{Size} & 5.00 & 3.00 & 3.00 & 1.00 & 3.50 & 4.00 & 11 \% \\
\hline
\textbf{Ease of Construction} & 3.00 & 5.00 & 3.00 & 1.00 & 4.00 & 2.00 & 13 \% \\
\hline
\textbf{Stability \& Control} & 0.00 & 5.00 & 1.00 & 3.00 & 2.00 & 1.00 & 21 \% \\
\hline
\textbf{Payload} & 0.00 & 0.00 & 0.00 & 0.00 & 0.00 & 0.00 & 12 \% \\
\hline
\textbf{Column Average} & \textbf{3.09} & \textbf{\underline{3.32}} & \textbf{2.65} & \textbf{1.30} & \textbf{2.93} & \textbf{2.63} & \\
\hline
\end{tabular}}
\label{tab:gear}
\end{table}

\newpage 

\section{Tail Configuration Matrix}
\label{sec:tail}
\begin{table}[h!]
\centering
\begin{tabular}{|c|c|c|c|c|}
\hline
& \textbf{Conventional} & \textbf{V-Tail} & \textbf{H-Tail} & \textbf{Bias}\\
\hline
\textbf{Weight} & 4.00 & 4.00 & 2.00 & 23 \%\\
\hline
\textbf{High L/D} & 5.00 & 5.00 & 2.00 & 20\%\\
\hline
\textbf{Size} & 3.00 & 3.00 & 2.00 & 11 \% \\
\hline
\textbf{Ease of Construction} & 5.00 & 2.00 & 5.00 & 13 \% \\
\hline
\textbf{Stability \& Control} & 4.00 & 2.00 & 5.00 & 21 \% \\
\hline
\textbf{Payload} & 3.00 & 3.00 & 3.00 & 12 \% \\
\hline
\textbf{Column Average} & \textbf{\underline{4.10}} & \textbf{3.29} & \textbf{3.14} & \\
\hline
\end{tabular}
\label{tab:tail}
\end{table}

\section{Motor Configuration Matrix}
\label{sec:motor}
\begin{table}[h!]
\centering
\begin{tabular}{|c|c|c|c|}
\hline
& \textbf{Mono-Tractor} & \textbf{Mono-Pusher} & \textbf{Bias}\\
\hline
\textbf{Weight} & 4.00 & 4.00 & 23 \%\\
\hline
\textbf{High L/D} & 4.00 & 2.00 & 20 \%\\
\hline
\textbf{Size} & 3.00 & 3.00 & 11 \% \\
\hline
\textbf{Ease of Construction} & 5.00 & 3.00 & 13 \% \\
\hline
\textbf{Stability \& Control} & 4.00 & 2.00 & 21 \% \\
\hline
\textbf{Payload} & 3.00 & 3.00 & 12 \% \\
\hline
\textbf{Column Average} & \textbf{\underline{3.90}} & \textbf{2.82}& \\
\hline
\end{tabular}
\label{tab:motor}
\end{table}
\end{appendices}
\end{document}

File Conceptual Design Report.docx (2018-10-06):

1. Mission and Design Proposal

The mission included 3 components. First, the aircraft must take off and maintain a low altitude flight path. Second, the aircraft climbs as high as possible over the course of a 10 second time interval and maintains level flight at the top. Finally, the aircraft must glide without power for as long as possible before reaching its original altitude prior to climb.

The primary design driver is weight and the secondary driver is a high lift to drag ratio (L/D). Reduced weight will help all aspects of the mission. Thus, it was determined to be most important. A high L/D will provide the aircraft with a good glide performance. This is because overall, the glide phase of the mission is to be optimized more than the climb phase.

The proposed design would have an aspect ratio of 5, a main wingspan of 5 feet, and a length of 3 feet. It would use a 1.25 horsepower motor and a 13 inch propellor with 8 degree pitch. It has a high wing for roll stability and a traditional tail for reduced weight.

2. Figure of Merit Analysis

The Figure of Merit (FoM) analysis is a tool that is used to address the choosing of components in an efficient and relatively objective manner. The FoM Analysis is not meant to produce aircraft details like wing aspect ratio, but the FoM will produce a numerical comparison between the major component types that are being considered for the aircraft. This is accomplished by choosing Figures of Merit based on our mission profile and primary and secondary design drivers.

Figure 1. Figure of Merits Table

| Weight | High L/D | Size | Ease of Construction | Stability & Control | Payload | Row Totals | Weight
Weight | 0.00 | 4.00 | 4.00 | 4.00 | 4.00 | 5.00 | 21.00 | 23.08
High L/D | 2.00 | 0.00 | 4.00 | 4.00 | 3.00 | 5.00 | 18.00 | 19.78
Size | 2.00 | 2.00 | 0.00 | 2.00 | 2.00 | 2.00 | 10.00 | 10.99
Ease of Construction | 2.00 | 2.00 | 4.00 | 0.00 | 1.00 | 3.00 | 12.00 | 13.19
Stability & Control | 3.00 | 3.00 | 4.00 | 5.00 | 0.00 | 4.00 | 19.00 | 20.88
Payload | 1.00 | 1.00 | 4.00 | 3.00 | 2.00 | 0.00 | 11.00 | 12.09
Column Total | | | | | | | 91.00 | 100

The figure of merits are then weighted against one another on a scale of 1 to 5 in order of importance to the design drivers. These numbers become the final weights for the component comparison. For each type of component, they are ranked from 1 to 5 in regard to the chosen figure of merits. This requires research on each component along with their advantages and disadvantages when applied to an aircraft. Each of these ranks are then weighted using the weights from the last step. Summing those weighted ranks give numerical justification for which component is most suited to the mission profile of the aircraft. Below is an example matrix of component comparison using this FoM analysis tool.

Figure 2. Wing Component Comparison Table

Monoplane | Biplane | Tandem Wing/Canard | Flying Wing/Blended Body | Winglets | Weight
4.00 | 3.00 | 3.00 | 5.00 | 5.00 | 0.23
3.00 | 4.00 | 3.00 | 3.50 | 2.00 | 0.20
3.00 | 1.00 | 3.00 | 4.00 | 5.00 | 0.11
5.00 | 2.00 | 2.00 | 1.00 | 5.00 | 0.13
4.50 | 3.00 | 2.00 | 1.00 | 1.00 | 0.21
3.00 | 3.00 | 3.00 | 1.50 | 3.00 | 0.12
3.80765 | 2.8461 | 2.6594 | 2.80785 | 3.33 | 1

The FoM analysis yielded some pretty standard results as far as a glider is concerned. The monoplane wing configuration was the highest ranked configuration due to its weight benefits and ease of construction. It also scored an average value in all the rest of the FoM categories. The conventional tail also ranked the highest for the same reasons. Since weight is our primary design driver, these components were valued much more highly over the others.

The tricycle landing gear component is not the lightest component, but it was chosen over lighter landing gear configurations for a few reasons. The most important reason is the ground take-off requirement imposed by the mission. Secondly, the tricycle landing gear is the most stable and provides a likelier chance of a successful take-off and landing. The power plant is a given component, and a tractor configuration is more desirable over a pusher configuration due to it’s static stability advantage.

3. Component Designs

Spreadsheets were used to determine numerical values for component sizing.

4. Predictions

Our team predicts that this design will be a performer in all aspects of the flight plan. It will have a decent climb rate and a good ability to takeoff. We expect the glide performance on this aircraft to be closer to exceptional than the other performance parameters. It is expected the glide performance will set this design apart from the competition.

Our empty weight is expected to be around 1.5 lbs which makes our estimated takeoff weight around 3.7 lbs. Our wing loading is estimated to be around 1.6 lbs/ft^2 which is on the low end of a glider aircraft. Our preliminary climb rate is estimated to be around 1100 ft/s which is a typical value for an aircraft with similar configuration as reported by previous senior design teams. We predict a glide rate of 2.5 ft/s and since our climb rate is 1100 ft/s, in 10 seconds of climb, we predict that we will glide for approximately 73 seconds. This is the ideal value for descent rate, but the actual performance will most likely be lower at about 60 seconds.

The spreadsheets predict a 272 feet take off distance and a landing distance of 1610 feet. Past experience tells us that these numbers are most likely inaccurate and will be much less than that. The predicted lift-to-drag ratio is approximately 26, which is in the realm of light cruise aircraft. We hope to bring this number up through some brainstorming in drag reduction methods in the future. In terms of stability and control, this aircraft will be utilizing conventional control surfaces, including, a rudder, 2 ailerons, and an elevator. This is sufficient for performing the given flight plan.

5. Summary

In conclusion, this aircraft is designed to be an all around performer with an emphasis on maximizing glide performance. This is accomplished by reducing the weight of the aircraft and achieving a high lift-to-drag ratio. This design features a minimalist fuselage due to the light payload requirements and has a circular for the benefits in drag reduction. The wing has an aspect ratio of 7 with a 5.5’ wingspan in order to balance the glide and climb portions of the flight. The FoM analysis pointed us towards a more conventional design for this aircraft. This will make the design easier to build and easier to fly, while still maintaining high performance and specification conformance.

6. Appendix

Figure 3. Control Surface Component Matrix

| 2x Ailerons, 2x Elevator, 2x Flaps | 2x Ailerons, 1x Elevators, 2x Flaps | 2x Ailerons, 2x Elevators | 2x Elevons | Row Totals | Weight
Weight | 1.00 | 2.00 | 3.00 | 5.00 | 11.00 | 0.23
High L/D | 5.00 | 4.00 | 3.00 | 1.00 | 13.00 | 0.20
Size | 1.00 | 2.00 | 3.00 | 5.00 | 11.00 | 0.11
Ease of Construction | 1.00 | 1.00 | 3.00 | 5.00 | 10.00 | 0.13
Stability & Control | 2.00 | 2.00 | 4.00 | 1.00 | 9.00 | 0.21
Payload | 0.00 | 0.00 | 0.00 | 0.00 | 0.00 | 0.12
Column Average | 1.879 | 2.0219 | 2.846 | 2.7695 | 54.00 | 1

Figure 4. Landing Gear Component Matrix

| None | Trike | Skids | Retractable | Tail Dragger | Monowheel | Weight
Weight | 5.00 | 3.00 | 4.00 | 1.00 | 3.50 | 4.00 | 0.23
High L/D | 5.00 | 3.00 | 4.00 | 1.00 | 4.00 | 4.00 | 0.20
Size | 5.00 | 3.00 | 3.00 | 1.00 | 3.50 | 4.00 | 0.11
Ease of Construction | 3.00 | 5.00 | 3.00 | 1.00 | 4.00 | 2.00 | 0.13
Stability & Control | 0.00 | 5.00 | 1.00 | 3.00 | 2.00 | 1.00 | 0.21
Payload | 0.00 | 0.00 | 0.00 | 0.00 | 0.00 | 0.00 | 0.12
Column Average | 3.0882 | 3.3185 | 2.6485 | 1.2965 | 2.92865 | 2.6265 | 1.00

Figure 5. Tail Configuration Component Matrix

| Conventional | V-Tail | H-Tail | | Weight
Weight | 4.00 | 4.00 | 2.00 | | 0.23
High L/D | 5.00 | 5.00 | 2.00 | | 0.20
Size | 3.00 | 3.00 | 2.00 | | 0.11
Ease of Construction | 5.00 | 2.00 | 5.00 | | 0.13
Stability & Control | 4.00 | 2.00 | 5.00 | | 0.21
Payload | 3.00 | 3.00 | 3.00 | | 0.12
Column Average | 4.0989 | 3.2858 | 3.1427 | | 1

Figure 6. Motor Configuration Component Matrix

| Mono Tractor | Mono Pusher | | Weight
Weight | 4.00 | 4.00 | | 0.23
High L/D | 4.00 | 2.00 | | 0.20
Size | 3.00 | 3.00 | | 0.11
Ease of Construction | 5.00 | 3.00 | | 0.13
Stability & Control | 4.00 | 2.00 | | 0.21
Payload | 3.00 | 3.00 | | 0.12
Column Average | 3.9011 | 2.8243 | | 1

[spreadsheets]

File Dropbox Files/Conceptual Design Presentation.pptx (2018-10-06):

## Conceptual Design

Brian Quinn, Mark Paluta, Eliseo Miranda, Pat Wall

## Design Drivers

1.) Low Weight
2.) High Lift/Drag (L/D)
Justification: Low weight helps all aspects of the mission. High L/D will help with glide.

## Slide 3

Figure of Merit (FOM) Analysis

| Weight | High L/D | Size | Ease of Construction | Stability & Control | Payload | Bias
Weight | 0.00 | 4.00 | 4.00 | 4.00 | 4.00 | 5.00 | 23 %
High L/D | 2.00 | 0.00 | 4.00 | 4.00 | 3.00 | 5.00 | 20 %
Size | 2.00 | 2.00 | 0.00 | 2.00 | 2.00 | 2.00 | 11 %
Ease of Construction | 2.00 | 2.00 | 4.00 | 0.00 | 1.00 | 3.00 | 13 %
Stability & Control | 3.00 | 3.00 | 4.00 | 5.00 | 0.00 | 4.00 | 21 %
Payload | 1.00 | 1.00 | 4.00 | 3.00 | 2.00 | 0.00 | 12 %
Column Total | | | | | | | 100 %

Key Factors: Weight, High Lift/Drag, Stability and Control

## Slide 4

FOM Analysis - Control Surface

| 2x Ailerons, 2x Elevator, 2x Flaps | 2x Ailerons, 1x Elevators, 2x Flaps | 2x Ailerons, 2x Elevators | 2x Elevons | Row Totals | Bias
Weight | 1.00 | 2.00 | 3.00 | 5.00 | 11.00 | 23 %
High L/D | 5.00 | 4.00 | 3.00 | 1.00 | 13.00 | 20 %
Size | 1.00 | 2.00 | 3.00 | 5.00 | 11.00 | 11 %
Ease of Construction | 1.00 | 1.00 | 3.00 | 5.00 | 10.00 | 13 %
Stability & Control | 2.00 | 2.00 | 4.00 | 1.00 | 9.00 | 21 %
Payload | 0.00 | 0.00 | 0.00 | 0.00 | 0.00 | 12 %
Column Average | 1.88 | 2.02 | 2.85 | 2.77 | 54.00 | 100 %

Best Result: 2x Ailerons, 2x Elevators

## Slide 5

FOM Analysis - Landing Gear

| None | Trike | Skids | Retractable | Tail Dragger | Monowheel | Bias
Weight | 5.00 | 3.00 | 4.00 | 1.00 | 3.50 | 4.00 | 23 %
High L/D | 5.00 | 3.00 | 4.00 | 1.00 | 4.00 | 4.00 | 20 %
Size | 5.00 | 3.00 | 3.00 | 1.00 | 3.50 | 4.00 | 11 %
Ease of Construction | 3.00 | 5.00 | 3.00 | 1.00 | 4.00 | 2.00 | 13 %
Stability & Control | 0.00 | 5.00 | 1.00 | 3.00 | 2.00 | 1.00 | 21 %
Payload | 0.00 | 0.00 | 0.00 | 0.00 | 0.00 | 0.00 | 12 %
Column Average | 3.09 | 3.32 | 2.65 | 1.30 | 2.93 | 2.63 | 100 %

Best Result: Trike Landing Gear

## FOM Analysis - Wing Configuration

| Monoplane | Biplane | Tandem Wing/Canard | Flying Wing/Blended Body | Winglets | Bias
Weight | 4.00 | 3.00 | 3.00 | 5.00 | 5.00 | 23 %
High L/D | 3.00 | 4.00 | 3.00 | 3.50 | 2.00 | 20 %
Size | 3.00 | 1.00 | 3.00 | 4.00 | 5.00 | 11 %
Ease of Construction | 5.00 | 2.00 | 2.00 | 1.00 | 5.00 | 13 %
Stability & Control | 4.50 | 3.00 | 2.00 | 1.00 | 1.00 | 21 %
Payload | 3.00 | 3.00 | 3.00 | 1.50 | 3.00 | 12 %
Column Average | 3.81 | 2.85 | 2.66 | 2.81 | 3.33 | 100 %

Best Result: Monoplane (Single Wing)

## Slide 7

FOM Analysis – Tail Configuration

| Conventional | V-Tail | H-Tail | Importance
Weight | 4.00 | 4.00 | 2.00 | 23 %
High L/D | 5.00 | 5.00 | 2.00 | 20 %
Size | 3.00 | 3.00 | 2.00 | 11 %
Ease of Construction | 5.00 | 2.00 | 5.00 | 13 %
Stability & Control | 4.00 | 2.00 | 5.00 | 21 %
Payload | 3.00 | 3.00 | 3.00 | 12 %
Column Average | 4.10 | 3.29 | 3.14 | 100 %

Best Result: Conventional Tail

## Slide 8

FOM Analysis - Engine

| Tractor | Pusher | Bias
Weight | 4.00 | 4.00 | 23 %
High L/D | 4.00 | 2.00 | 20 %
Size | 3.00 | 3.00 | 11 %
Ease of Construction | 5.00 | 3.00 | 13 %
Stability & Control | 4.00 | 2.00 | 21 %
Payload | 3.00 | 3.00 | 12 %
Column Average | 3.90 | 2.82 | 100 %

Best Result: Tractor Configuration

## Important Quantities from Spreadsheets

Aspect ratio = 7
Span = 5’ 6”
Length = 3’
Takeoff Weight = 3.7 lbs

## Conceptual CAD Model

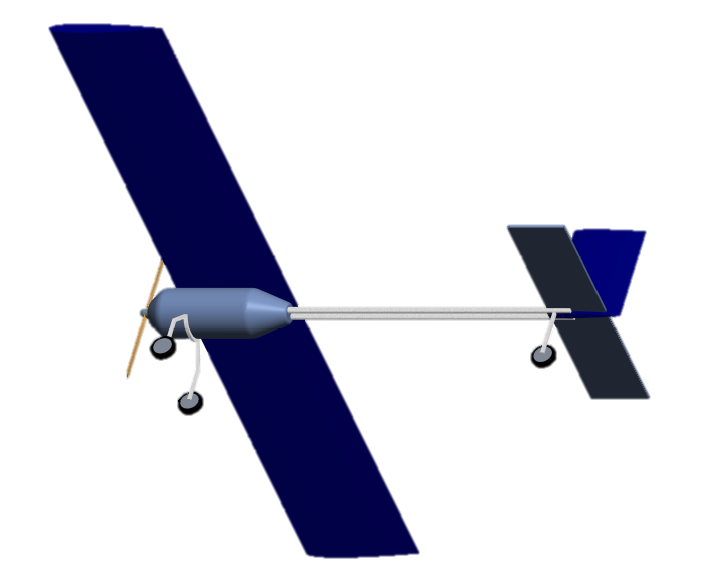
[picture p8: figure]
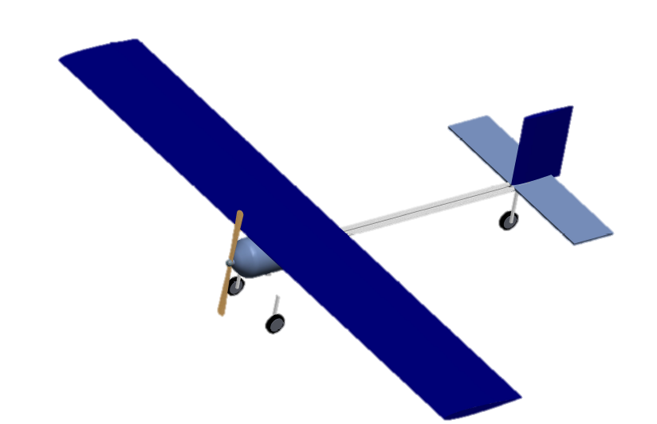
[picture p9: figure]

## Performance Predictions

Climb rate of 18.3 ft/s (for 10 s)
Descent rate of 2.5 ft/s

→ Glide time of 73 s

## Summary

- We seek to optimize primarily glide rate, and secondarily climb rate.
- Primary design driver is weight
- Secondary design driver is L/D

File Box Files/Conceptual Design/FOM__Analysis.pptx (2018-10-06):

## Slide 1

| Weight | High L/D | Size | Ease of Construction | Stability & Control | Payload Capability | Totals | Weight (%)
Weight | 0 | 4 | 4 | 4 | 4 | 5 | 21
High L/D | 2 | 0 | 4 | 4 | 3 | 5 | 18
Size | 2 | 2 | 0 | 2 | 2 | 2 | 10
Ease of Construction | 2 | 2 | 4 | 0 | 1 | 3 | 12
Stability & Control | 3 | 3 | 4 | 5 | 0 | 4 | 19
Payload Capability | 1 | 1 | 4 | 3 | 2 | 0 | 11

## Control Surface Configuration

Control Surface Configuration | Weight (%) | 2x Ailerons, 2x Elevator, 2x Flaps | 2x Ailerons, 1x Elevator, 2x Flaps | 2x Ailerons, 2x Elevator | 2x Elevons
Weight | | 1 | 2 | 3 | 5
High L/D | | N/A | N/A | N/A | N/A
Size | | N/A | N/A | N/A | N/A
Ease of Construction | | N/A | N/A | N/A | N/A
Stability & Control | | 5 | 4 | 4 | 2
Payload Capability | | N/A | N/A | N/A | N/A
Total

## Landing Gear Configuration

Landing Gear Configuration | Weight (%) | None | Trike | Skids | Retractable | Tail Dragger | Mono Wheel
Weight | | 5 | 3 | 4 | 1 | 3.5 | 4
High Lift/Short Takeoff | | 1 | 3 | 1 | 3 | 3 | 2
Size | | 5 | 3 | 3 | 1 | 3.5 | 3
Ease of Construction | | 5 | 5 | 3 | 1 | 4 | 3
Stability & Control | | 0 | 5 | 1 | 3 | 2 | 1
Payload Capacity | | 4 | 3 | 3 | 1 | 2 | 3
Total

## Wing Configuration

Wing Configuration | Weight (%) | Monoplane | Biplane | Tandem Wing / Canard | Flying Wing / Blended Body
Weight | | 4 | 3 | 3 | 5
High L/D | | 3 | 4 | 3 | 3.5
Size | | 3 | 1 | 3 | 4
Ease of Construction | | 5 | 2 | 2 | 1
Stability & Control | | 4.5 | 3 | 2 | 1
Payload Capability | | 3 | 3 | 3 | 1.5
Total

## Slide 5

Empennage Configuration | Weight (%) | Conventional Tail | V-Tail | H-Tail | Winglets
Weight | | 4 | 4 | 2 | 5
High L/D | | 5 | 5 | 2 | 2
Size | | 3 | 3 | 2 | 5
Ease of Construction | | 5 | 2 | 5 | 5
Stability & Control | | 4 | 2 | 5 | 1
Payload | | 3 | 3 | 3 | 3
Total

## Motor Configuration

Motor Configuration | Weight (%) | Mono Tractor | Mono Pusher
Weight | | 4 | 4
High L/D | | 4 | 2
Size | | 3 | 3
Ease of Construction | | 5 | 3
Stability & Control | | 4 | 2
Payload Capability | | 3 | 3
Total

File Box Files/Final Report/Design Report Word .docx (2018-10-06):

1 Introduction

For years, remotely-controlled aircraft have captured the interests of hobby enthusiasts of all ages and skillsets, combining ease of operation with a multitude of designs available as kits, templates, or ready-made models. For students at the university level, however, who have had exposure to flight principles like aerodynamics, dynamics, and fluid mechanics, scale aircraft provide a unique opportunity to translate that theory into a physical application at relatively low costs, allowing students to explore untested design concepts and construction ideas in an environment that celebrates challenges and mishaps as an opportunity to learn.

It is this concept that inspired the 2014 senior design capstone project for which students were tasked with working cohesively as a team to construct viable aircraft, complete with useable control surfaces, guided by their knowledge of aerodynamics concept and the skills of seasoned pilots. Steered by a mission mandate requiring that each aircraft be designed to climb to as high an altitude as possible in ten seconds before performing an unpowered glide back down to the cruising altitude, the four students of DBC Industries, referred to herein as the Team, created an aircraft colloquially referred to as, ``The Flappy Bird", a minimalist airframe designed to climb quickly while also allowing the craft to glide for long periods of time. This report details the design and construction process of the final vehicle and also analyzes the results of preliminary flight testing, permitting a comparison of predicted vehicle maneuverability and the observed capabilities during flight.

2 Mission and Design Proposal

The stated mission for this design project consists of three phases of aircraft flight operation. The aircraft must first take off, solely under its own power, and maintain low altitude, level flight. From there, it must begin to climb as fast and as high as it can over a ten second interval and level off at the top of its ascent. After circling at the new altitude and verifying its stability, the aircraft will perform an unpowered glide back to its original altitude, with the area of focus centered on the rate of descent during that glide.

The primary design driver for this mission profile was aircraft weight. Weight savings were gained from efficient design of the wing and fuselage structures to eliminate excess material weight. A low weight helped with both of the main objectives of the mission, climb and glide. For climb, a low-weight structure did not tax the fixed-thrust propeller motor as much as a heavier aircraft would on vertical ascent. On the gliding descent as well, a lighter aircraft experienced a more favorable descent gradient than heavier variants using the same lifting surfaces.

The secondary design driver was a high lift-to-drag (L/D) ratio. High performance in this area will promote a low descent rate during the gliding phase of flight, allowing the aircraft to remain aloft for an extended period of time. In this design, the glide performance was deemed the mission phase in most need of optimization and, as such, the choice of the two primary design drivers centers around the aircraft performance characteristics that will lead to the best glide performance.

1

There are a few key physical features on the proposed aircraft that served as main drivers towards the desired mission objectives. The main wing has an aspect ratio of 7, leading to a total wingspan of 5 feet, 6 inches. The high aspect ratio contributed to a low wing loading during descent which was favorable for glide performance. The wing was mounted high on the fuselage to afford the aircraft increased roll stability during flight.

3 Figure of Merit Analysis

Although this design was ultimately constrained by the requirements of the mission statement, a determination of favorable attributes for an aircraft of this type was conducted using a figure of merit (FoM) analysis. An FoM analysis is part of a design approach that is used to select components that form an aircraft’s structure in an efficient and objective manner. Although the analysis cannot produce design dimensions, it can provide a numerical point of comparison between different variations of airframe components under consideration. As Table I shows, physical and performance characteristics are evaluated across a rating system between 1 and 5, with larger numbers representing a greater importance to the design drivers. The row totals are then summed and each characteristic is assigned a bias percentage which determines its overall priority in the final design.

Table I: Figures of Merit for Aircraft Performance

| Weight | High L/D | Size | Ease of Construction | Stability & Control | Payload | Row Totals | Bias
Weight | 0.00 | 4.00 | 4.00 | 4.00 | 4.00 | 5.00 | 21.00 | 23 %
High L/D | 2.00 | 0.00 | 4.00 | 4.00 | 3.00 | 5.00 | 18.00 | 20 %
Size | 2.00 | 2.00 | 0.00 | 2.00 | 2.00 | 2.00 | 10.00 | 11 %
Ease of Construction | 2.00 | 2.00 | 4.00 | 0.00 | 1.00 | 3.00 | 12.00 | 13 %
Stability & Control | 3.00 | 3.00 | 4.00 | 5.00 | 0.00 | 4.00 | 19.00 | 21 %
Payload | 1.00 | 1.00 | 4.00 | 3.00 | 2.00 | 0.00 | 11.00 | 12 %

Once the design biases have been set, the figure of merit analysis was conducted on each of the possible component configurations considered for the final design. Table II illustrates the process for the main wing selection. Unlike Table I, component analyses ratings are based on each configuration’s benefit or detriment to the stated design drivers, with larger numbers representing more beneficial performance. These rankings are

2

based on research into each possible configuration with special care taken to identify the strengths and weaknesses of each design. To finally determine the most appropriate component variation for the mission profile, a weighted average of the figures of merit for each configuration was tabulated, appearing on the bottom row of the matrix. Matrices for each of the other component analyses are located in Appendices A-D

Table II: Wing Design Matrix

| Monoplane | Biplane | Tandem Wing/Canard | Flying Wing/Blended Body | Winglets | Bias
Weight | 4.00 | 3.00 | 3.00 | 5.00 | 5.00 | 23 %
High L/D | 3.00 | 4.00 | 3.00 | 3.50 | 2.00 | 20 %
Size | 3.00 | 1.00 | 3.00 | 4.00 | 5.00 | 11 %
Ease of Construction | 5.00 | 2.00 | 2.00 | 1.00 | 5.00 | 13 %
Stability & Control | 4.50 | 3.00 | 2.00 | 1.00 | 1.00 | 21 %
Payload | 3.00 | 3.00 | 3.00 | 1.50 | 3.00 | 12 %
Column Average | 3.81 | 2.85 | 2.66 | 2.81 | 3.33

The results of each analysis were not entirely unexpected given the common history of these types of aircraft. Table II shows that the single wing is the most advantageous wing configuration because of its low weight and relative ease of construction. Beyond those, it also boasts a high level of stability and average scores in all of the remaining categories, highlighting it as the best possible configuration.

Scoring highly in the same categories as the wing, the conventional tail also logged a markedly higher score than its competitors. Historical data comparisons show that the conventional tail has the lowest weight of the three variations in the category and, due to its right angle mounted design, scores well for ease of construction as well.

The final component selection of note is that of the landing gear. Historically, the three wheel trike configuration has a heavier under-mount system than other options such as the skids and tail gear which would suggest that it would conflict with the primary design driver of weight. In this instance, however, the additional stability gained over other gear options provided enough justification to the team to prioritize stability over weight. In addition to stability advantages, the trike gear also provides the aircraft with a more forgiving structure on which to land and takeoff. The three wheel configuration elevates the underbelly off the ground and provides some level of shock absorption during landing, preventing damage to the fuselage or lifting surfaces.

3

4 Predictions from Spreadsheet Analysis

In addition to the figure of merit analysis, the provided aircraft design spreadsheets were used to determine finite numerical dimensions for each of the airframe components as well as providing some insight into the forces acting on the vehicle during flight.

Our empty weight is expected to be around 1.5 pounds, leading to an estimated takeoff weight of approximately 3.7 pounds which is a typical weight based on previous senior design aircraft. This figured is based on a preliminary weight estimate consisting of 2 pounds of aircraft control and monitoring equipment and a vehicle structure factor of 0.4.

Perhaps one of the most important factors for determining the aircraft’s ability to perform well within the mission constraints is the wing loading as it is an integral factor in the aircraft’s climb and glide performance. As mentioned previously, glide performance is the mission phase in most need of optimization and, as such, the wing loading on the vehicle was determined based on performance during descent, during which a low wing loading is desired. True to form, assuming a glide from 1,400 ft ,assuming a ground elevation of 729 feet in South Bend, the wing loading during glide would only amount to about 0.81 lb/ft2, or approximately 13 oz/ft2, a wing loading that will surely help contribute to satisfactory glide performance.

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

Each spreadsheet used in this analysis is attached at the back of this report in the order of completion. Due to the constraints and requirements of this remote controlled aircraft, the engine and flap spreadsheets have been omitted. Please note the following as well: The takeoff and landing spreadsheet is not representative of the values expected during either phase of flight and quantities cited in both the refined weight and stability

4

analyses are rough estimates and will be updated throughout construction with actual values.

5 Detailed Design

The aircraft wing was the most challenging, and arguably most important, aspect of the design. The wing aspect ratio had to be small enough for decent climb and performance large enough for decent glide performance. The wing had a final span of 5.5 feet and an aspect ratio of 6.7. The compromise between these two decisions made it such that design team had to innovate in other areas of the design in order to be a truly competitive aircraft, rather than an average one. That is the reason why weight was such an important factor in the success of this plan.

The fuselage and wing had to be strong enough to withstand the high stress of take off and landing while also light enough to be competitive. For this reason, a rectangular carbon fiber rod was chosen as the main structural element of the fuselage. It was meant to take most of the stress in flight and as the backbone of the fuselage and tail assemblies. Weight savings were gained from the need for less material due to the functionality of the carbon fiber rod. The fuselage was approximately cylindrical, tapering off in roughly a cone at the trailing edge. It housed most of the internal electronics, aside from two aileron servos and a pitot tube in the main wing. The propeller mounted to a thick bulkhead at the flat leading edge of the fuselage.

The main landing gear was attached directly to the carbon fiber rod within the fuselage. Since the main landing gear experiences the most stress of any other component, it was beneficial to transfer that energy to the strongest part of the aircraft. It was also reinforced with plywood around the edges of the connection to prevent the gear from torqueing off of the carbon fiber tube. The aircraft was made a tail dragger to decrease weight and improve take-off performance. A small wheel was attached directly to the rudder to reduce the amount of mechanical linkages. This negligibly reduced the ground control of the aircraft but improved weight characteristics, which was more desirable for the given mission profile.

The tail was of conventional design placed on a boom tail. One of the concerns for this type of design was the twist of the boom tail. This was counteracted with a double thick carbon fiber rod as well as double thick ply for stiffness of the assembly as a whole and individual material, as well. A custom bracket was designed for the attachment of the tail surfaces to the carbon fiber. Each surface had two anchor points to prevent twisting and was held in place with epoxy. The elevator and rudder control surfaces were large enough for sufficient control of the aircraft and had no flutter or twist in-flight.

The design employed a 1.25 horsepower motor, capable of providing approximately 3.5 pounds-force of thrust. This gave a final thrust-to-weight ratio of 0.7. This motor powered a 13-inch propeller with an 8-inch pitch. The main wing was mounted atop the fuselage and bolted on, utilizing hatches to access internal components. This high wing configuration contributed to roll stability, as indicated in conceptual design. For further details on the design, see the attached CAD drawings.

6 Results

The results were calculated from a combination of the two runs. The average flight speed was 34.2 mph. The maximum and minimum flight speeds attained were 52.8 and 20.0 mph respectively. The maximum climb rate was 22.6 ft/s and the average was 19.3 ft/s. The minimum glide rate was -7.7 ft/s and the average was -8.6 ft/s. From the observed results and the predicted ones, the success factor was calculated to be 3.7. The ideal success factor was 15.8.

7 Discussion

Overall, this aircraft performed very well for the given mission profile. The aircraft was designed such that it balanced the climb and glide portions of the flight in an efficient way. The design team decided that the most important factor for a balanced design was reducing the total weight. This proved to be a correct decision when compared to other designs with the same mission profile. The thrust to weight ratio of the aircraft was approximately 1. This allowed the plane to climb at a much faster pace than competitive aircraft, giving it more time to glide.

8 Conclusion

Overall, this aircraft performed very well for the given mission profile.

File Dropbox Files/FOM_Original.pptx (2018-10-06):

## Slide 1

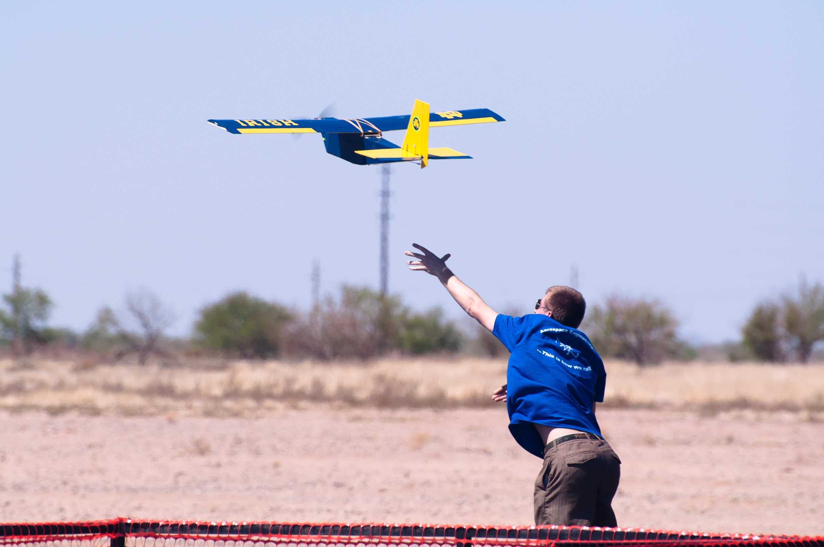
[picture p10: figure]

FOM Analysis
Design, Build, Fly!

9/15/13

## Missions Review

  - Backcountry Rough Field Bush Plane
  - Pre-Flight Rough Field Taxi Mission
  - Mission 1 – Complete as many laps as possible in 4 minutes
  - Mission 2 – 3 lap max load flight – 6”x6”x6” wood blocks
  - Mission 3 – Emergency Medical Mission – 3 lap, prescribed load
  - Competition in Wichita, KS

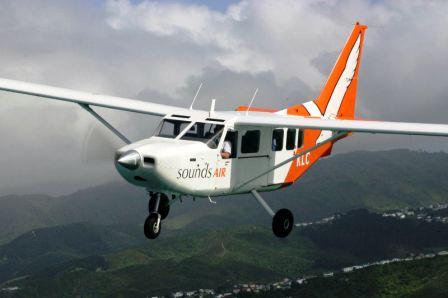
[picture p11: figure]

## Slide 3

Scoring Analysis Conclusions

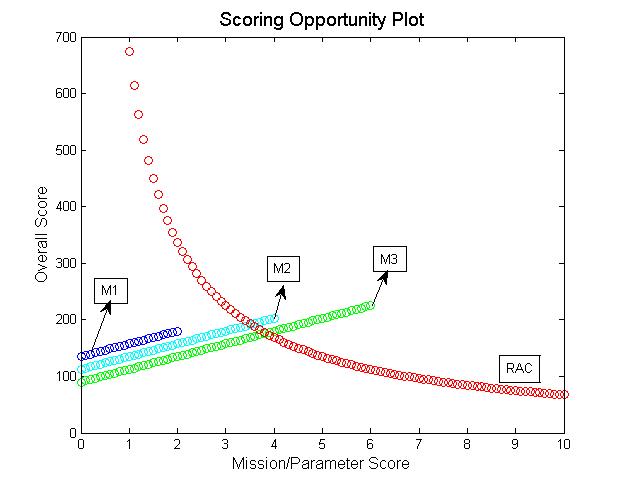
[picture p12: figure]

## Design Drivers

Scoring Analysis Conclusions

Sample Competition Scenarios

- Primary: Empty Weight
- Secondary: Speed

Fast and Light Plane

- M1 = 1.7 – M2=1.5 – M3=5.8
- RAC=2.5
- Final Score = 324

Large Towing Capacity

- M1 = 1.1 – M2=4 – M3=4
- RAC=4
- Final Score = 204.75 -- (if RAC=5, Score=163.8)

Renaissance Plane

- M1 = 1.45 – M2=3 – M3=5
- RAC=3.5
- Final Score = 243.00

## Figure of Merit Weights

| Weight | High Lift/Short TO | Glide Capability | Size | Ease of Construction | Stability & Control | Payload Capability | Totals | Weight (%)
Weight | 0 | 3 | 2 | 4 | 4 | 4 | 4 | 23 | 18.25
High Lift/Short Takeoff | 3 | 0 | 2 | 2 | 2 | 1 | 3 | 12 | 9.5
Glide Capability | 4 | 4 | 0 | 4 | 5 | 3 | 5 | 24 | 19.06
Size | 2 | 4 | 2 | 0 | 2 | 2 | 2 | 14 | 11.12
Ease of Construction | 2 | 4 | 1 | 4 | 0 | 1 | 2 | 14 | 11.12
Stability & Control | 2 | 5 | 3 | 4 | 5 | 0 | 4 | 23 | 18.25
Payload Capability | 2 | 3 | 1 | 4 | 4 | 2 | 0 | 16 | 12.7
| | | | | | | | 126

## Figure of Merit Weights

Figure of Merit | Weight (%)
Weight
Short-Take Off/High Lift
Speed
Size
Payload Capability
Stability & Control
Ease of Construction

## Wing Configuration

Wing Configuration | Weight (%) | Monoplane | Biplane | Tandem Wing / Canard | Flying Wing / Blended Body
Weight | 18.25 | 4 | 3 | 3 | 5
High Lift/Short Takeoff | 9.5 | 3 | 4 | 3 | 3.5
Speed | 19.06 | 4 | 2 | 3 | 4.5
Size | 11.12 | 3 | 1 | 3 | 4
Ease of Construction | 11.12 | 5 | 2 | 2 | 1
Stability & Control | 18.25 | 4.5 | 3 | 2 | 1
Payload Capability | 12.7 | 3 | 3 | 3 | 1.5
Total | 100% | 3.87 | 2.57 | 2.71 | 3.03

## Motor Configuration

Motor Configuration | Weight (%) | Mono Tractor | Mono Pusher | Twin Tractor | Twin Pusher | Tractor & Pusher
Weight | 18.25 | 4 | 4 | 2 | 2 | 2
High Lift/Short Takeoff | 9.5 | 4 | 2 | 5 | 1 | 2
Speed | 19.06 | 4 | 3 | 5 | 4 | 4
Size | 11.12 | 3 | 3 | 2 | 2 | 2
Ease of Construction | 11.12 | 5 | 3 | 2 | 1 | 1
Stability & Control | 18.25 | 4 | 2 | 3 | 1 | 1
Payload Capability | 12.7 | 3 | 3 | 3 | 3 | 3
Total | | 3.87 | 2.86 | 3.17 | 2.12 | 2.21

## Tail Configuration

Empennage Configuration | Weight (%) | Conventional Tail | V-Tail | Single Vertical Stabilizer | Winglets
Weight | 18.25 | 4 | 4 | 3 | 5
High Lift/Short Takeoff | 9.5 | 5 | 5 | 1 | 2
Speed | 19.06 | 3 | 4 | 3 | 4
Size | 11.12 | 3 | 3 | 4 | 5
Ease of Construction | 11.12 | 5 | 2 | 5 | 5
Stability & Control | 18.25 | 5 | 2 | 1 | 1
Payload | 12.7 | 3 | 3 | 3 | 3
Total | 100% | 3.96 | 3.27 | 2.78 | 3.54

## Landing Gear Configuration

Landing Gear Configuration | Weight (%) | None | Trike | Skids | Retractable | Tail Dragger | Mono Wheel
Weight | 18.25 | 5 | 3 | 4 | 1 | 3.5 | 4
High Lift/Short Takeoff | 9.5 | 1 | 3 | 1 | 3 | 3 | 2
Speed | 19.06 | 5 | 3 | 4 | 3.5 | 3.5 | 4
Size | 11.12 | 5 | 3 | 3 | 1 | 3.5 | 3
Ease of Store Construction | 11.12 | 5 | 5 | 3 | 1 | 4 | 3
Stability & Control | 18.25 | 0 | 5 | 1 | 3 | 2 | 1
Total | 100 | 3.07 | 3.2 | 2.4 | 1.9 | 2.8 | 2.5

## Control Surface Configuration

Control Surface Configuration | Weight (%) | 2x Ailerons, 2x Elevator, 2x Flaps | 2x Ailerons, 1x Elevator, 2x Flaps | 2x Ailerons, 2x Elevator | 2x Elevons
Weight | 13.10 | 1 | 2 | 3 | 5
High Lift/Short Takeoff | 9.52 | N/A | N/A | N/A | N/A
Glide Rate | 16.67 | 3 | 3 | 3 | 3
Size | 9.52 | N/A | N/A | N/A | N/A
Ease of Construction | 9.52 | N/A | N/A | N/A | N/A
Stability & Control | 14.88 | 5 | 4 | 4 | 2
Payload Capability | 10.12 | N/A | N/A | N/A | N/A
Climb Rate | 16.70 | 5 | 5 | 5 | 4
Total | 100% | 3.5 | 3.5 | 3.75 | 3.5

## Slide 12

2013-2014

Pilots
Terry Rensberger
Paul Distler

University of Notre Dame
AIAA DBF

Faculty Advisor
TBD

Graduate Advisors
Annie Legault
Tamuto Takakura

Team Leads
Harrison Yates
Eliseo Miranda

Report Lead
Eliseo Miranda/Harrison Yates

Aerodynamics Lead
Kate Disser

TBD

Structures / CAD Lead
Keldan Mulvey

TBD

Propulsion / Electronics Lead
Joshua Vahala

Construction/Testing Lead
Tom Paulius

TBD

TBD

TBD

## Organization

- All students now have 50GB worth of cloud storage within Box
  - https:// (https://notredame.box.com/files)notredame.box.com/files
  - Invites to the DBF “Box” will be sent shortly
    - Used for all team data storage (Report files, CAD files, pictures, etc.)
- Machine Shop Training
  - Laser Cutter, Safety, 3D Printer
- Weekly Meetings
  - Sunday @ 4:30pm
  - Stinson-Remick 109

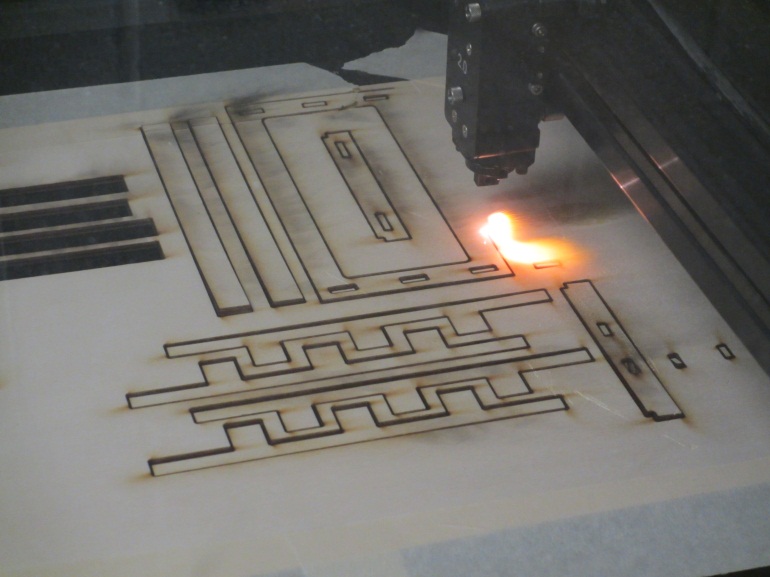
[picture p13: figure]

## Notre Dame Design/Build/Fly

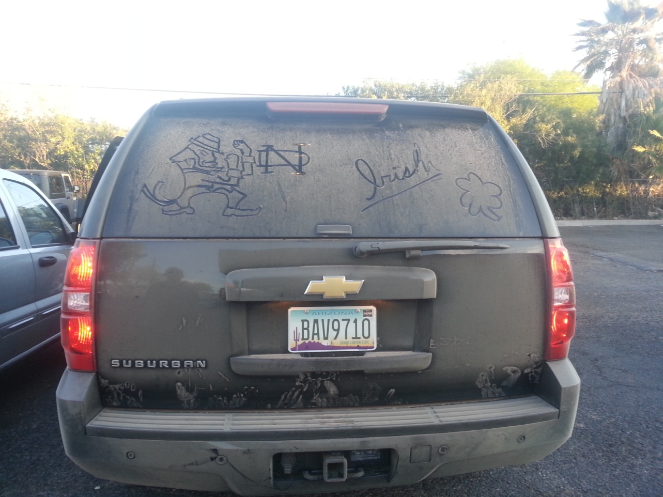
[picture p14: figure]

Questions?

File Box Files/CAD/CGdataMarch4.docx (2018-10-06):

MASS = 3.6270829e+00 POUND

CENTER OF GRAVITY with respect to ACS0 coordinate frame:

X Y Z 7.5097411e+00 2.0338456e-01 2.1800318e-02 INCH

MASS PROPERTIES OF COMPONENTS OF THE ASSEMBLY

(in assembly units and the ACS0 coordinate frame)

DENSITY MASS C.G.: X Y Z

FUSELAGE_RIB MATERIAL: LITE-PLY

1.38900e-02 7.12499e-03 2.50000e+00 7.52317e-02 2.22045e-16

FUSELAGE_RIB MATERIAL: LITE-PLY

1.38900e-02 7.12499e-03 7.50000e+00 7.52317e-02 2.22045e-16

FUSELAGE_RIB MATERIAL: LITE-PLY

1.38900e-02 7.12499e-03 1.25000e+01 7.52317e-02 2.22045e-16

FUSELAGE_STRINGER MATERIAL: STRINGERS

2.65000e-02 8.21036e-03 7.50000e+00 -9.16603e-01 1.47112e+00

FUSELAGE_STRINGER MATERIAL: STRINGERS

2.65000e-02 8.21036e-03 7.50000e+00 1.43548e+00 1.54468e+00

FUSELAGE_STRINGER MATERIAL: STRINGERS

2.65000e-02 8.21036e-03 7.50000e+00 1.43548e+00 -1.54468e+00

FUSELAGE_STRINGER MATERIAL: STRINGERS

2.65000e-02 8.21036e-03 7.50000e+00 1.64800e+00 -6.90000e-01

FLOOR_W_PARTS MATERIAL: UNKNOWN

4.99299e-02 1.02070e+00 3.35868e+00 1.31530e-01 8.68996e-02

FUSELAGE_STRINGER MATERIAL: STRINGERS

2.65000e-02 8.21036e-03 7.50000e+00 1.64800e+00 6.90000e-01

FUSELAGE_STRINGER MATERIAL: STRINGERS

2.65000e-02 8.21036e-03 7.50000e+00 3.00000e-01 1.91297e+00

FUSELAGE_STRINGER MATERIAL: STRINGERS

2.65000e-02 8.21036e-03 7.50000e+00 3.00000e-01 -1.91297e+00

FUSELAGE_STRINGER MATERIAL: STRINGERS

2.65000e-02 8.21036e-03 7.50000e+00 -9.16603e-01 -1.47112e+00

NOSE_STRINGER MATERIAL: LITE-PLY

1.38900e-02 2.44706e-02 1.21922e+00 1.45575e-01 -1.12940e-03

NOSE_CONE MATERIAL: LITE-PLY

1.38900e-02 2.09715e-02 1.25000e-01 1.66533e-15 2.22045e-16

MOTOR_PLATE MATERIAL: AL6061

9.79121e-02 5.04772e-02 -7.95000e-02 4.87117e-06 2.22045e-16

MOTOR_MOUNT MATERIAL: UNKNOWN

1.12000e-01 7.30223e-01 -1.23400e+00 4.87117e-06 2.22045e-16

PROPELLER MATERIAL: PROPELLER

1.70800e-01 8.60024e-02 -2.53902e+00 4.87399e-06 2.22045e-16

TAIL_ASSEMBLY MATERIAL: UNKNOWN

1.37724e-02 6.16538e-01 3.26689e+01 -2.08960e-01 -2.57517e-03

WING_ASSEMBLY MATERIAL: UNKNOWN

1.59847e-02 3.69483e-01 9.25186e+00 2.27538e+00 -3.52962e-05

FUSELAGE_BACK_PLATE MATERIAL: LITE-PLY

1.38900e-02 1.29793e-02 1.41964e+01 5.13044e-01 2.22045e-16

MAIN_GEAR_ASSY MATERIAL: UNKNOWN

1.03300e-02 6.81837e-02 5.62500e-01 -4.53603e+00 -1.96500e-01

PAYLOAD MATERIAL: UNKNOWN

2.25000e+00 5.40000e-01 8.62500e-01 2.75000e-01 1.00000e-02

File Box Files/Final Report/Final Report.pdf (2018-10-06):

# Design and Flight Analysis of the Remote-Controlled

# Flappy Bird Aircraft

Brian Quinn, Mark Paluta, Eliseo Miranda, Patrick Wall

May 9, 2014

Abstract

Scale model, remotely-controlled aircraft are used extensively for hobby pilots, but also serve a secondary,

educative purpose of allowing university students to apply aerodynamic theory to a physical flight application.

In this design project, a high aspect ratio, low wing loading aircraft was designed to fly a mission in which it

would be required to fly to high altitudes before performing an unpowered descent back to its cruising altitude.

Implementing performance characteristics calculated using principles of fluid mechanics and aerodynamics,

along with historical data from previous designs, the team of student engineers designed a minimalist vehicle,

constructed from light woods and carbon fiber, that demonstrated speeds of up to 48 mph with climb rates as high as 1246 ft/min to meet the mission requirements, surpassing pre-flight predictions. Although flight

data indicates that glide predictions far exceeded the observed values, the plane was able to successfully

progress through each phase of the mission profile without issue and proved to be both maneuverable and

well-controlled in the air, leaving the designers with confidence that subsequent design iterations would allow

those performance issues to be resolved.

Design and Flight Analysis of the Remote-Controlled Flappy Bird Aircraft | 1

## Contents

List of Figures | 1
List of Tables | 1
1 Introduction | 2
2 Mission Profile | 2
3 Detailed Design | 2
4 Predictions from Spreadsheet Analysis | 5
5 Flight Test Results | 7
6 Discussion | 8
7 Conclusion | 10
Appendices | 12
Appendix A Figure of Merit Analysis | 12
Appendix B Design Guidance Spreadsheets | 15

## List of Figures

1 | Isometric view of CAD model highlighting minimalist airframe structure | | 3
2 | Dimensioned model of the main wing depicting rib structure as well as airfoil shape and
| positioning | | 5
3 | Tail design detailing important dimensions and weight-saving structural designs | | 6
4 | Flappy Bird aircraft seconds after completion | | 7
5 | Climb and descent profiles flown by the Flappy Bird aircraft during two flight tests | | 8
6 | Speed of Flappy Bird aircraft measured by onboard sensors throughout flight test | | 9

## List of Tables

I | Figures of Merit for Aircraft Performance | | 12
II | Wing Design Matrix | | 12
III | Control Surface Component Matrix | | 13
IV | Landing Gear Component Matrix | | 13
V | Tail Configuration Matrix | | 14
VI | Motor Configuration Matrix | | 14

Design and Flight Analysis of the Remote-Controlled Flappy Bird Aircraft | 2

## 1 Introduction

For years, remotely-controlled aircraft have captured the interests of hobby enthusiasts of all ages

and skillsets, combining ease of operation with a multitude of designs available as kits, templates, or ready-

made models. For students at the university level, however, who have had exposure to flight principles

like aerodynamics, dynamics, and fluid mechanics, scale aircraft provide a unique opportunity to translate

that theory into a physical application at relatively low costs, allowing students to explore untested design

concepts and construction ideas in an environment that celebrates challenges and mishaps as an opportunity

to learn.

It is this concept that inspired the 2014 senior design capstone project for which students were tasked

with working cohesively as a team to construct viable aircraft, complete with useable control surfaces, guided

by their knowledge of aerodynamics concept and the skills of seasoned pilots. Steered by a mission mandate

requiring that each aircraft be designed to climb to as high an altitude as possible in ten seconds before

performing an unpowered glide back down to the cruising altitude, the four students of DBC Industries,

referred to herein as the Team, created an aircraft colloquially referred to as, “The Flappy Bird”, a minimalist

airframe designed to climb quickly while also allowing the craft to glide for long periods of time. This report

details the design and construction process of the final vehicle and also analyzes the results of preliminary

flight testing, permitting a comparison of predicted vehicle maneuverability and the observed capabilities

during flight.

## 2 Mission Profile

The mission profile for this design project, as alluded to previously, consists of three distinct phases

of flight operation. In Phase I, the aircraft must take off under its own power and maintain low altitude,

level flight while its stability and control are verified by the remote pilot. Pending a successful checkout, the

aircraft then proceeds to Phase II in which it must begin to climb to as high an altitude as possible in a

ten second interval. From there, Phase III begins with a short period of high altitude, level flight before the

craft returns to its original altitude through an unpowered glide, with focus placed on the rate of descent of

the aircraft.

## 3 Detailed Design

Before construction began on the physical aircraft, an exhaustive design process was undertaken to

ensure the mission requirements could be met during flight testing, guided by the designation of two primary

design drivers. Of utmost concern was the aircraft’s overall weight. Although the aircraft was required to

carry data collection sensors and servo motors to drive the control surface deflections, the Team chose a

minimalist approach to the design of the fixed structure. Unlike service aircraft which require a rigid, metal

skin around the fuselage and wing surfaces, the conditions under which these scale aircraft flew exacted

far less stress on the airframe, allowing large portions of the structure, that might otherwise be covered in

wood sheeting, to be replaced with monokote, a plastic covering that bonds to materials when heated. As

Design and Flight Analysis of the Remote-Controlled Flappy Bird Aircraft | 3

the CAD model in Figure 1 shows, the elimination of rigid skin allowed the Team to use wood only where

necessary to defined the shape of the airframe or to provide a surface onto which sensors and other payloads

could rest. These material savings along with use of light woods such as balsa and spruce allowed the Team


Figure 1: Isometric view of CAD model highlighting minimalist airframe structure

to construct a robust aircraft with a low structure weight, putting less stress on the motor during climb and

requiring less of the wing during the descent glide.

To further address the issue of weight, a rectangular carbon fiber rod was chosen as the main structural

element of the fuselage. As the backbone for both the fuselage and tail assemblies, the rod would take most

of the stress on the airframe during flight, but would do so with minimal added weight. The fuselage was

approximately cylindrical, tapering off in roughly a cone at the trailing edge and built up from the carbon

fiber rod that ran through the length of its underbelly. It also housed most of the internal electronics with

the exception of two aileron servos and a pitot tube in the main wing. Protruding from the front of the

fuselage structure was a double-thick bulkhead upon which the motor and propeller assembly were affixed.

Located under the fuselage and epoxied directly to the front end of the carbon fiber rod, the main

landing gear, experienced the most stress of any component on the aircraft due to its direct impact with the

ground on landing attempts, and thus was attached strongest part of the aircraft allowing the gear system

to transfer energy out of its legs upon impact. The connection points to the fuselage were also reinforced

with a plywoord box, epoxied to the carbon fiber on both sides of the gear, to prevent any torquing motions

Design and Flight Analysis of the Remote-Controlled Flappy Bird Aircraft | 4

from ripping the gear off of the aircraft. At the aft end of the aircraft, a small, steerable wheel was attached

directly to the rudder, reducing the number of mechanical linkages and improving the takeoff performance

due to the increase angle of attack of the wing while rolling on the ground. Attaching the wheel to the

rudder negligibly reduced the ground control of the aircraft but improved weight characteristics, which was

more desirable for the given mission profile.

The secondary driver employed in this design was a high lift-to-drag performance ratio. As outlined

in the course textbook, a high lift force with a correspondingly low drag force promotes a lower descent rate

during the gliding phase of flight, allowing the aircraft to remain aloft for proportionally longer periods of

time. Although drag is a phenomena affecting all parts of the aircraft structure, the design of the main wing

was of greatest concern to the Team as it has the largest overall effect on the ratio and, consequently, was

the most challenging and, arguably, most important aspect of the design.

Climb and glide are located at the opposite ends of the design spectrum when seeking an optimimum

aspect ratio for a main wing. A small aspect ratio will help with climb and maneuverability while a large

aspect ratio increases the performance during glide. To address each of these, an aspect ratio of 7 was

selected to strike a mean between the two extremes, leading to a total wing span of 66 inches and a constant

chord length of 9.6 inches. These design characteristics were implemented using a Clark Y flat-bottom airfoil.

Used extensively in remote-controlled aircraft applications, the flat bottom afforeded the Team the ability

to attach a mounting plate to the underside of the wing, allowing it to rigidly screw down onto the fuselage

structure. The Clark Y also has the advantage of excellent lifting qualities at the low to middle range angles

of attack at which the aircraft would be flying. A detailed drawing depicting the Clark Y shape and the rib

structure of the aircraft can be found below in Figure 2 which also highlights the dimensions of the main

wing structure.

The tail was of conventional design placed at the free end of the carbon fiber rod protruding from

the fuselage as seen in Figure 1. One of the main concerns of this design, however, was the potential for

severe torquing from the lift forces generated by the tail surfaces. Addressing these issues early in the

design process, the thickness of the carbon fiber rod was doubled, as was the thickness of the plywood used

to construct the tail surfaces, leading to structurally sound design as seen in Figure 3 below, which also

highlights the main dimensions, in inches, of the horizontal and vertical tail surfaces. A custom bracket

was designed for the attachment of the tail surfaces to the carbon fiber, and each tail surface was anchored,

using epoxy, to the bracket at two locations, thus preventing twisting. The elevator and rudder control

surfaces were overdesigned to provide more than sufficient control of the aircraft and prevent flutter or twist

in-flight. Although Figure 3 shows large holes in the tail surface, these were monokoted over in the final

design, allowing weight savings without any detriment to performance.

Rouding out the design, the aircraft used a 1.25 horsepower motor, capable of providing approximately

3.5 pounds-force of thrust. With a final takeoff weight of 5 pounds, including a 0.84 pound payload, this

yielded a final thrust-to-weight ratio of 0.7. The motor powered a 13-inch propeller with an 8-inch pitch

which created the power to move the craft through the air. As the main wing was bolted onto the fuselage

before flight, hatches in both the top and side of the fuselage were used to allow access to internal components

without removing the wing. The final flight vehicle is shown below in Figure 4 in a picture taken just seconds

after the final component of the fuselage was added, completing the craft.

Design and Flight Analysis of the Remote-Controlled Flappy Bird Aircraft | 5
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

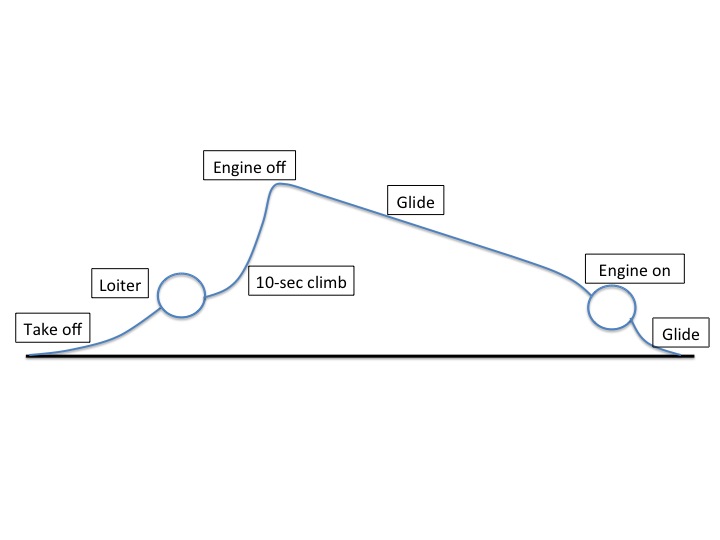
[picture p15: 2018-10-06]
Box Files/Final Report/mission_profile/Slide1.jpg

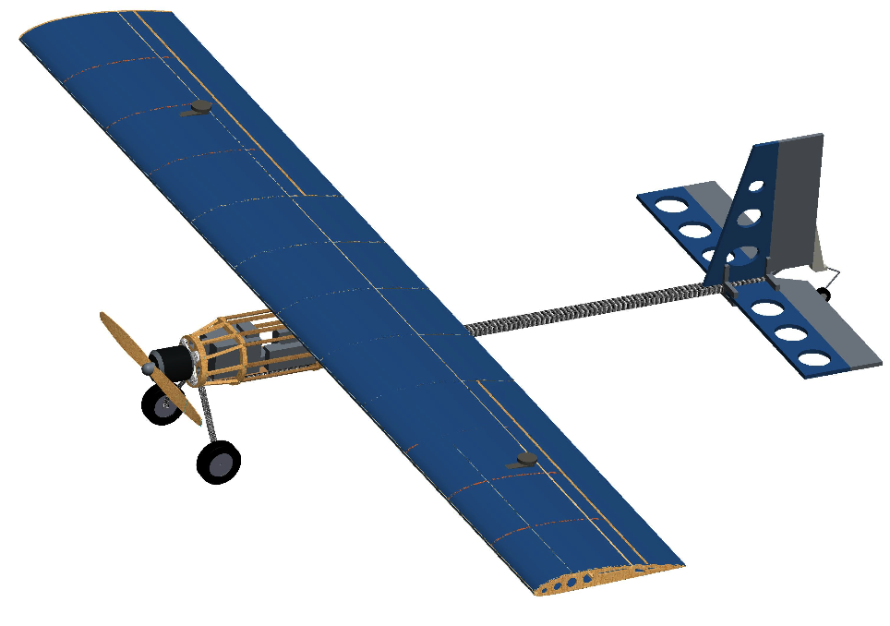
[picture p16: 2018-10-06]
Box Files/Final Report/CAD_Full_Skin.png

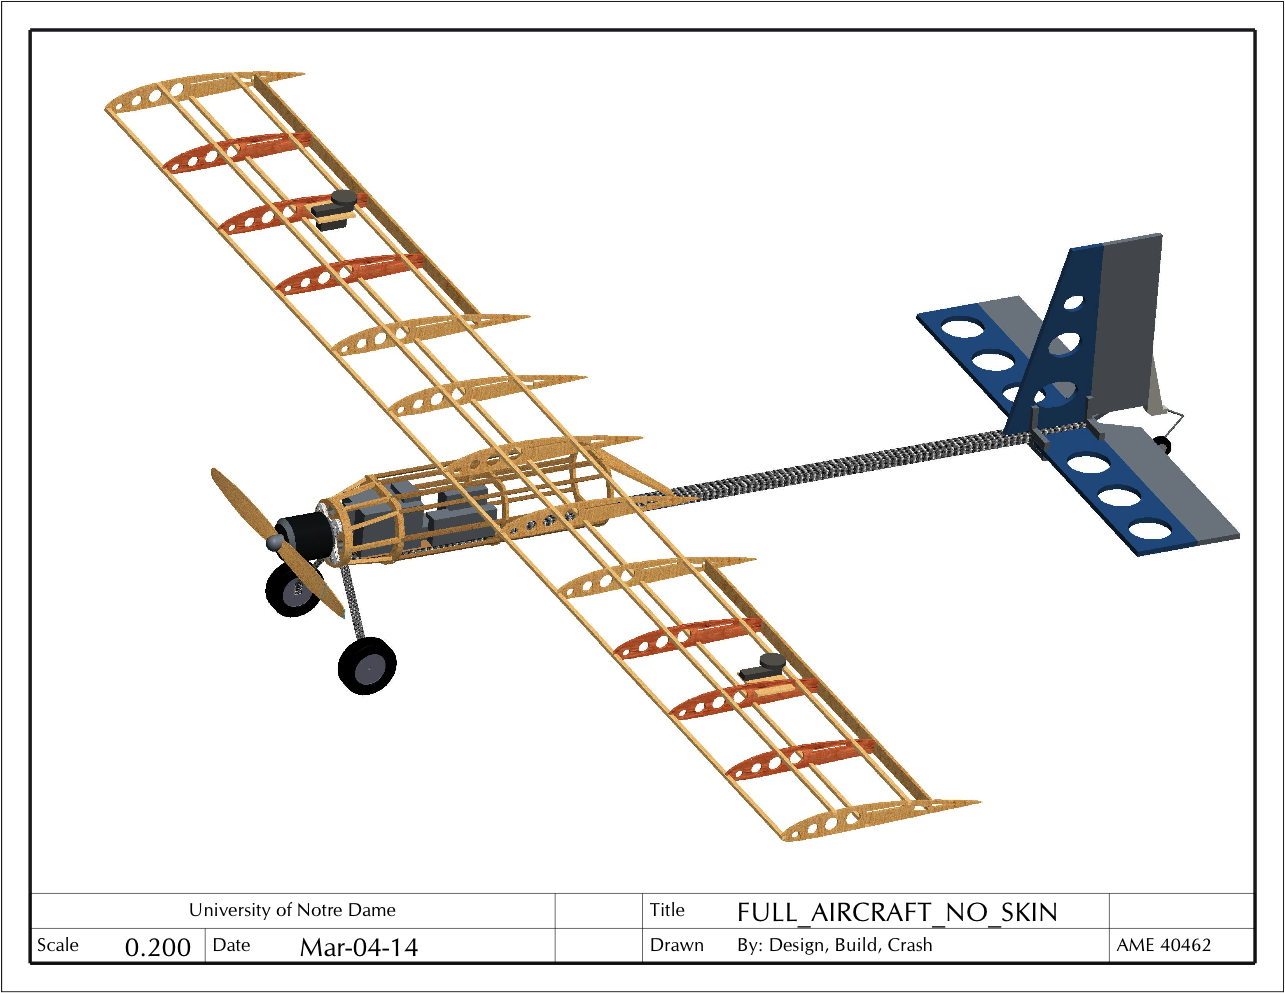
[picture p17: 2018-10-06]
Box Files/Final Report/Full_NoSkin.png

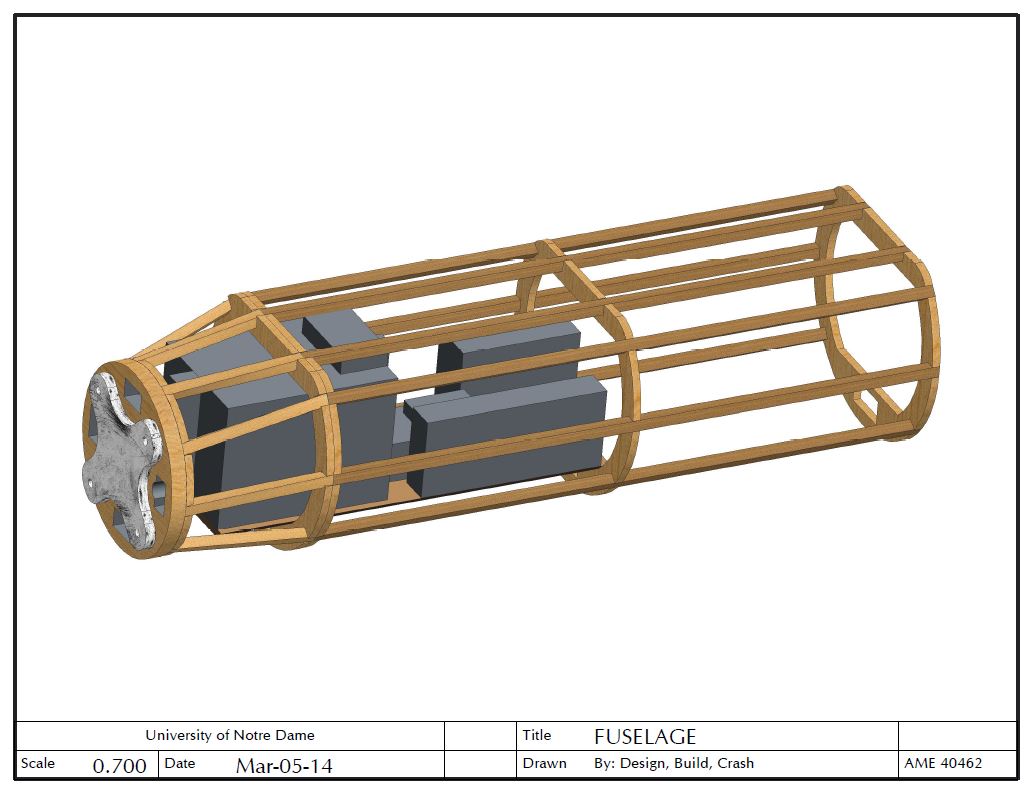
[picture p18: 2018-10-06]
Box Files/CAD/Fuselage.JPG

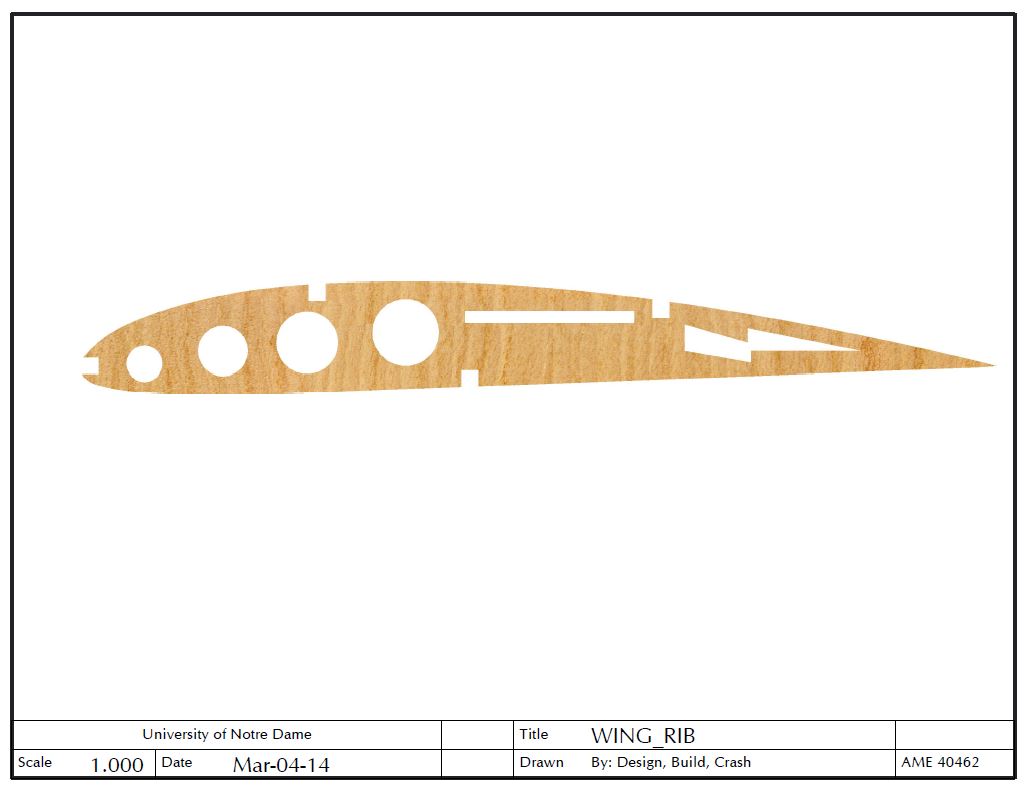
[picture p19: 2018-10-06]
Box Files/CAD/Wing Rib.JPG

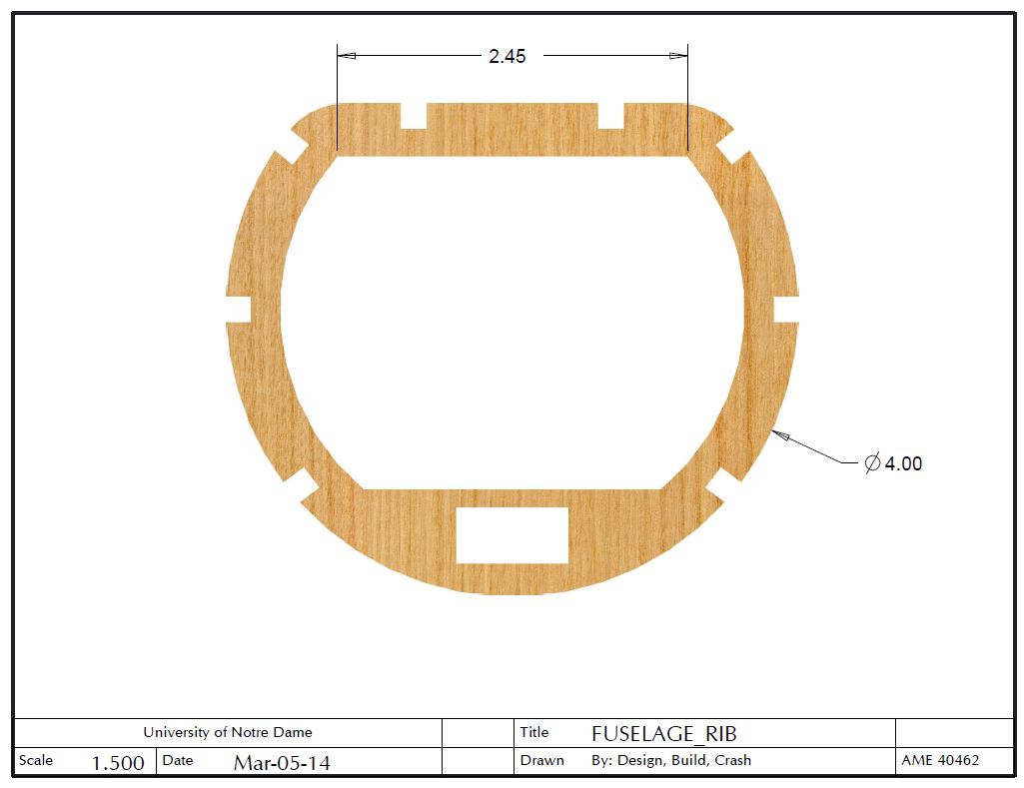
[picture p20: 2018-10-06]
Box Files/CAD/Fuselage Rib.JPG

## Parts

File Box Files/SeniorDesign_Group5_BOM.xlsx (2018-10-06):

Part Number | Part Name | QTY | Vendor | Cost (each) | URL Address
LXHV38 | Top Flite MonoKote Cub Yellow 6' | 1 | Tower Hobbies | $13.99 | http://www3.towerhobbies.com/cgi-bin/wti0001p?&I=LXHV38&P=ML | $13.99
LXHV20 | Top Flite MonoKote Orange 6' | 1 | Tower Hobbies | $13.99 | http://www3.towerhobbies.com/cgi-bin/wti0001p?&I=LXHV20&P=ML
LXHV22 | Top Flite MonoKote Jet White 6' | 1 | Tower Hobbies | $13.99 | http://www3.towerhobbies.com/cgi-bin/wti0001p?&I=LXHV22&P=ML
NPN | 1/8 x 12 x 24 lite ply | 18 | National Balsa | $3.62 | http://www.nationalbalsa.com/lite_ply_p/181224lp.htm
NPN | 1/8 x 4 x 36 Aero Light Balsa | 5 | National Balsa | $4.08 | http://www.nationalbalsa.com/Aero_Light_Balsa_p/18436ct.htm
NPN | 3/8X2-1/2X48 AILERON STOCK | 4 | National Balsa | $3.10 | http://www.nationalbalsa.com/Aileron_p/3821248as.htm
NPN | 3/16 x 36 dowels | 4 | National Balsa | $0.23 | http://www.nationalbalsa.com/product_p/31636do.htm
NPN | 3/8 x 48 dowels | 5 | National Balsa | $0.61 | http://www.nationalbalsa.com/product_p/3848do.htm
NPN | 3/16x3/16x48 sitka spruce sticks | 10 | National Balsa | $1.50 | http://www.nationalbalsa.com/Spruce_Stick_p/31631648ss.htm
NPN | 1/16x10-1/2x48 balsa wing skins | 6 | National Balsa | $7.80 | http://www.nationalbalsa.com/product_p/116101248.htm
NPN | 3/16 x 3/16 x 48 basswood stick | 20 | National Balsa | $0.77 | http://www.nationalbalsa.com/basswood_p/31631648b.htm
20-423 | Carbon Fiber Square Rods (10mm x 8.5mm x 1000mm) | 4 | RC Foam | $17.90 | http://www.rcfoam.com/carbon-fiber-sheets%2C-carbon-rods-and-tubes/square-carbon-tubes-for-remote-control-planes/carbon-square-tube-p-844.html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
20-501 | Carbon Fiber Landing Gear Legs, Mini Electric Plane | 1 | RC Foam | $11.79 | http://www.rcfoam.com/carbon-fiber-sheets%2C-carbon-rods-and-tubes/carbon-hobby-parts-for-radio-controlled-airplanes-for-sale/airplane-accessories-p-855.html
LXV47 | Sullivan Tailwheel Bracket 40-60 5-12 lbs | 1 | Tower Hobbies | $9.99 | http://www3.towerhobbies.com/cgi-bin/wti0001p?&I=LXFV47&P=C
LXB908 | Dave Brown Lite Flite Wheel 2-1/2" | 2 | Tower Hobbies | $5.99 | http://www3.towerhobbies.com/cgi-bin/wti0001p?&I=LXB908&P=C
LXFU87 | Sullivan T-2 Tail Wheel 1" | 2 | Tower Hobbies | $2.09 | http://www3.towerhobbies.com/cgi-bin/wti0001p?&I=LXFU87&P=M
LXD812 | Dubro Tail Wheel 1" | 1 | Tower Hobbies | $1.89 | http://www3.towerhobbies.com/cgi-bin/wti0001p?&I=LXD812&P=M
LXE097 | Dubro Nylon Wing Bolts 1/4-20x2 | 3 | Tower Hobbies | $1.03 | http://www3.towerhobbies.com/cgi-bin/wti0001p?&I=LXE097&P=7
LXE060 | Dubro Nylon Insert Locknuts 1/4-20 | 3 | Tower Hobbies | $1.31 | http://www3.towerhobbies.com/cgi-bin/wti0001p?&I=LXE060&P=7

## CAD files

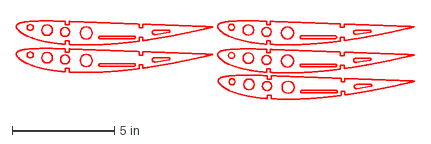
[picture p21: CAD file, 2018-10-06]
Box Files/CAD/Current Senior Design CAD/full_wing_ribs.dxf
19.5 x 3.83 in

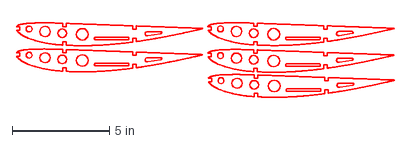
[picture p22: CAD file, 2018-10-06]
Box Files/CAD/Current Senior Design CAD/full_wing_ribs2.dxf
19.4 x 3.83 in

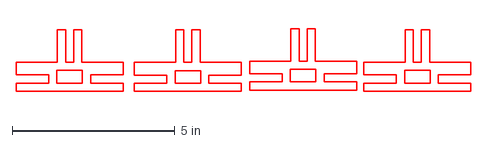
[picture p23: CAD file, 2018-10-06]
Box Files/CAD/Current Senior Design CAD/tail_block.dxf
14.0 x 1.93 in

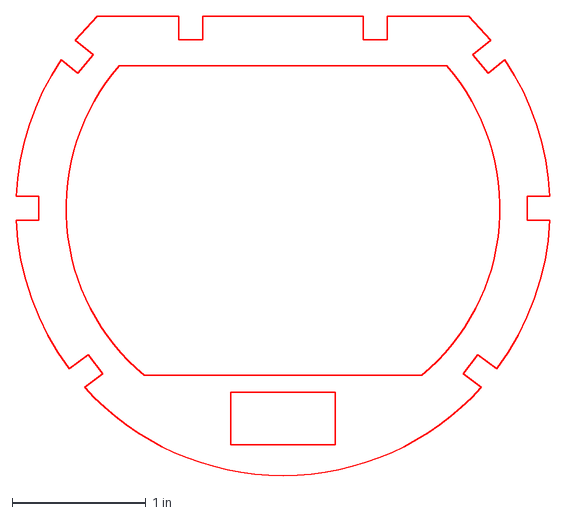
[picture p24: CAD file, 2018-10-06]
CAD March4 (backup)/fuse_rib.dxf
4.00 x 3.44 in

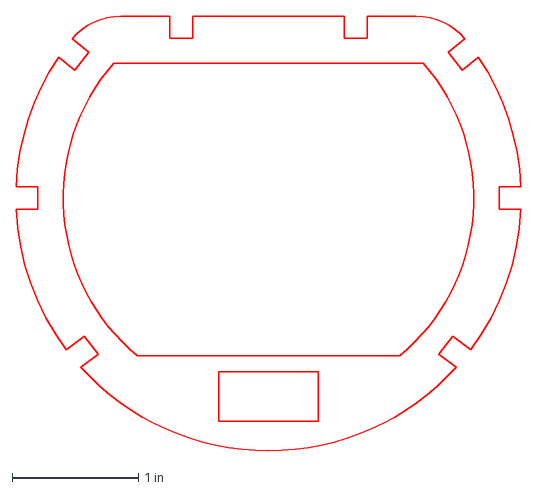
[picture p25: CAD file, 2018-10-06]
Box Files/CAD/Current Senior Design CAD/fuselage_rib.dxf
4.00 x 3.44 in

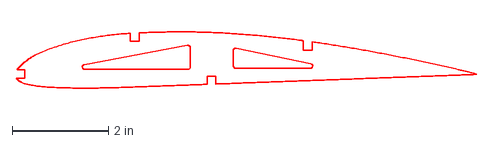
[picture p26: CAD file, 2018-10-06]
CAD March4 (backup)/wing_rib2.dxf
9.57 x 1.17 in

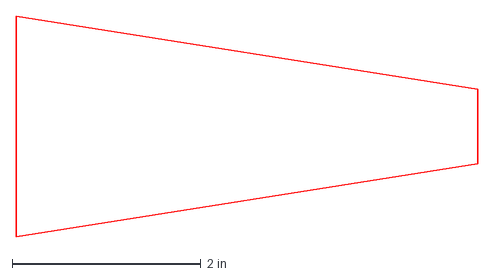
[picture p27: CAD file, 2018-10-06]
Box Files/CAD/Current Senior Design CAD/fuselage_back_plate.dxf
4.89 x 2.34 in

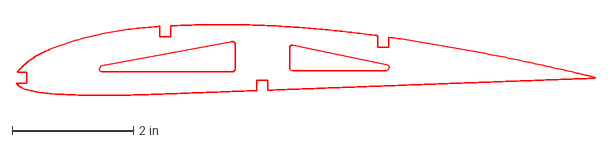
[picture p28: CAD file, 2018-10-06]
CAD March4 (backup)/wing_rib.dxf
9.57 x 1.17 in

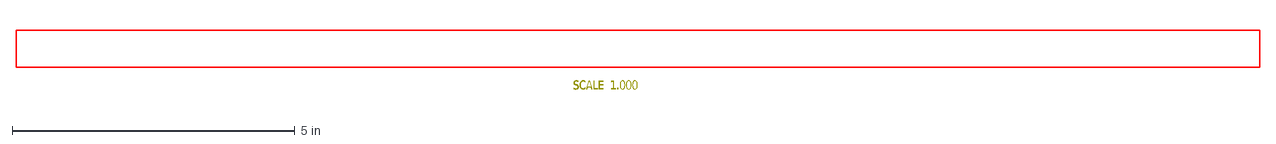
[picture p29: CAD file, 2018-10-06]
Box Files/CAD/Current Senior Design CAD/aileron_plate.dxf
SCALE 1.000

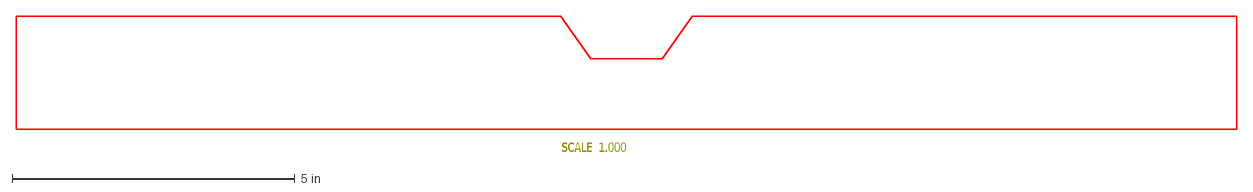
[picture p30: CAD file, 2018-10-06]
Box Files/CAD/Current Senior Design CAD/elevator.dxf
SCALE 1.000

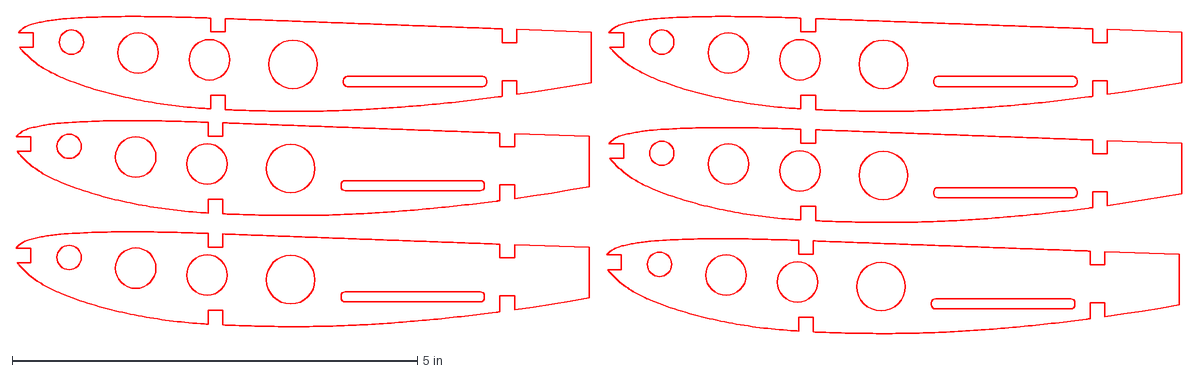
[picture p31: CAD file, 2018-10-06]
Box Files/CAD/Current Senior Design CAD/wing_aileron_ribs2.dxf
14.4 x 3.91 in

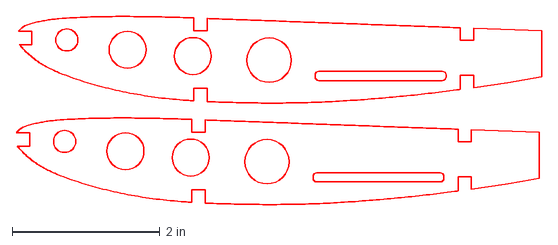
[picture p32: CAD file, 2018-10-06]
Box Files/CAD/Current Senior Design CAD/wing_aileron_ribs_ply.dxf
7.10 x 2.54 in

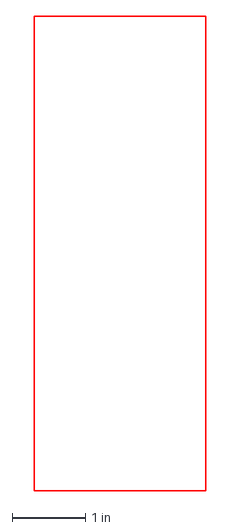
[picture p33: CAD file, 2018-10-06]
Box Files/CAD/Current Senior Design CAD/floor.dxf
2.35 x 6.50 in

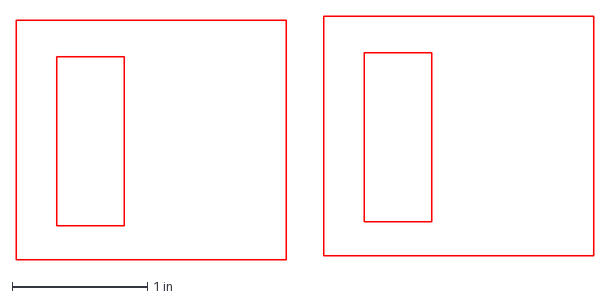
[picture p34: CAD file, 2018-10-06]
Box Files/CAD/Current Senior Design CAD/servo_mount_plate2.dxf
4.28 x 1.80 in

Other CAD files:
Box Files/CAD/Current Senior Design CAD/wing_attachment_plate.dxf
Box Files/CAD/Current Senior Design CAD/fuse_ribs.dxf
Box Files/CAD/Current Senior Design CAD/wing_aileron_ribs.dxf
Box Files/CAD/Current Senior Design CAD/fuselage_ribs.dxf
Box Files/CAD/Current Senior Design CAD/bulkhead_front.dxf
Box Files/CAD/Current Senior Design CAD/bulkhead_secondary.dxf
Box Files/CAD/Current Senior Design CAD/horizontal_plate.dxf
Box Files/CAD/Current Senior Design CAD/rudder.dxf
Box Files/CAD/Current Senior Design CAD/vertical_plate.dxf
Box Files/CAD/Current Senior Design CAD/wing_plate_fuselage.dxf
Box Files/CAD/Current Senior Design CAD/wing_ribss.dxf

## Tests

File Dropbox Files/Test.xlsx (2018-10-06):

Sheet: IterTow
 | Mission Requirements
Max. Mach | 0.04
Cruise Mach | 0.04
Cruise Alt. (ft) | 1000
Oper. Rad. (nm) | 0.5
Engine: TSFC Min. | 0
Engine: TSFC Max. | 0
Engine: Thrust (lbs) | 3
Aspect Ratio | 7
Combat: Time (min) | 0
Combat: Altitude (ft) | 0
Loiter: Time (min) | 0
Loiter: Altitude (ft) | 0
Fuel Reserve (%) | 0
Trapped Fuel (%) | 0
Structure Factor | 0.4
Payload: Exp. (lb) | 0
Payload: Non-exp. (lb) | 2
 |  | Iteration 1 | Iteration 2 | Iteration 3 | Iteration 4 | Iteration 5 | Iteration 6 | Iteration 7
Weight: T-O (estimated) | 3 | 3.00 | 3.35 | 3.64 | 3.64 | #DIV/0! | #DIV/0! | #DIV/0!
Weight: T-O (final) |  | 3.35 | 3.51 | 3.64 | 3.64 | #DIV/0! | #DIV/0! | #DIV/0!
Surplus Empty Wt. (lbs) |  | -0.35 | -0.16 | 0.00 | 0.00 | #DIV/0! | #DIV/0! | #DIV/0!
1. Start-up & T-O |  | 2.92 | 3.27 | 3.55 | 3.55 | #DIV/0! | #DIV/0! | #DIV/0!
2. Climb & Accel. to Cruise |  | 2.92 | 3.26 | 3.55 | 3.55 | #DIV/0! | #DIV/0! | #DIV/0!
3a. L/D |  | 17.00 | 17.00 | 17.00 | 17.00 | 17.00 | 17.00 | 17.00
3b. V (f/s) |  | 44.02 | 44.02 | 44.02 | 44.02 | 44.02 | 44.02 | 44.02
3c. Cruise to destination |  | 2.92 | 3.26 | 3.55 | 3.55 | #DIV/0! | #DIV/0! | #DIV/0!
4. Accel. to high speed |  | 2.92 | 3.26 | 3.55 | 3.55 | #DIV/0! | #DIV/0! | #DIV/0!
5. Combat |  | 2.92 | 3.26 | 3.55 | 3.55 | #DIV/0! | #DIV/0! | #DIV/0!
6. Drop Exp. Payload |  | 2.92 | 3.26 | 3.55 | 3.55 | #DIV/0! | #DIV/0! | #DIV/0!
7. Cruise back |  | 2.92 | 3.26 | 3.55 | 3.55 | #DIV/0! | #DIV/0! | #DIV/0!
7. Loiter |  | 2.92 | 3.26 | 3.55 | 3.55 | #DIV/0! | #DIV/0! | #DIV/0!
8. Land |  | 2.85 | 3.18 | 3.46 | 3.46 | #DIV/0! | #DIV/0! | #DIV/0!
Total Fuel Wt. (lbs) |  | 0.15 | 0.17 | 0.19 | 0.19 | #DIV/0! | #DIV/0! | #DIV/0!
Available Empty Wt. (lbs) |  | 0.85 | 1.18 | 1.46 | 1.46 | #DIV/0! | #DIV/0! | #DIV/0!
Required Empty Wt. (lbs) |  | 1.20 | 1.34 | 1.46 | 1.46 | #DIV/0! | #DIV/0! | #DIV/0!

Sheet: WingLD
Take-off |  | Landing
H (f) | 692 | H (f) | 692
CL(max) | 1.6 | CL(max) | 1.6
T(max) (lb) | 2.9258 | T(max) (lb) | 2.9258
W_TO (lb) | 3.64229727 | W_L (lb) | 3.456918908
S (f^2) | 4.354978219 | W/S (lb/f^2) | 0.7937855793
W/S (lb/f^2) | 0.8363525802 | S (f^2) | 4.354978219
SIGMA | 0.9819042 | SIGMA | 0.9819042
T/W | 0.8032842416 | T/W | 0.8463606113
TOP | 0.6627214897 | LP | 0.5052590538
S_TO (f) | 77.32831904 | S_TO (f) | 459.6205684
Cruise Start |  | Cruise End
CD_0 | 0.015 | CD_0 | 0.015
A | 7 | A | 7
H (f) | 1000 | H (f) | 1000
Cruise Mach | 0.04 | Cruise Mach | 0.04
W (lb) | 3.55 | W (lb) | 3.545557854
k | 0.0568410511 | k | 0.0568410511
V (f/s) | 44.024 | V (f/s) | 44.024
rho (lbm/f^3) | 0.0744742049 | rho (lbm/f^3) | 0.0744742049
q (lbf/f^2) | 2.241294924 | q (lbf/f^2) | 2.241294924
W/S (lb/f^2) | 0.8141390557 | W/S_optimum | 0.8141390557
S (f^2) | 4.354978219 | W/S_actual | 0.8141390557
Climb |  | Acceleration
H (f) | 1000 | H (f) | 50
Climb Mach | 0.04 | Cruise Mach | 0.04
dH/dt (f/min) | 1100 | n | 5
V (f/s) | 44.024
G (rad) | 0.4164395178 | V (f/s) | 44.1532
Gamma (deg) | 24.61000254 | rho (lbm/f^3) | 0.07637401024
rho (lbm/f^3) | 0.0744742049 | q (lbf/f^2) | 2.311980127
q (lbf/f^2) | 2.241294924 | W/S (lb/f^2) | 0.2375355805
T/W min | 0.475
T/W min - G | 0.05839917008
W/S_+ (lb/f^2) | 1.151366529
W/S_- (lb/f^2) | 1.15136646
Turn - Inst. |  | Turn- Sustained
H (f) | 1000 | H (f) | 1000
Cruise Mach | 0.04 | Cruise Mach | 0.04
CL_max | 1.6 | n | 5
W/S (lb/f^2) | 0.8141390557 | W/S (lb/f^2) | 0.8141390557
V (f/s) | 44.024 | T/W_max | 0.2919958504
rho (lbm/f^3) | 0.0744742049 | V (f/s) | 44.024
q (lbf/f^2) | 2.241294924 | rho (lbm/f^3) | 0.0744742049
psi_dot (rad/s) | 3.137587754 | q (lbf/f^2) | 2.241294924
psi_dot (deg/s) | 179.770688 | psi_dot (rad/s) | 2.441465502
n | 4.404741246 | psi_dot (deg/s) | 139.8857873
Ceiling |  | Descent
W (lb) | 3.55 | W (lb) | 3.545557854
S (f^2) | 4.354978219 | S (f^2) | 4.354978219
H (f) | 900 | H (f) | 1400
Cruise Mach | 0.04 | Cruise Mach | 0.04
W/S (lb/f^2) | 0.8141390557 | W/S (lb/f^2) | 0.8141390557
V (f/s) | 44.0376 | V (f/s) | 43.9696
rho (lbm/f^3) | 0.07467418441 | rho (lbm/f^3) | 0.07367428686
q (lbf/f^2) | 2.248701996 | q (lbf/f^2) | 2.211745248
CL_required | 0.3620484427 | dH/dt-min (f/min) | 150.5928187
 |  | Gamma (deg) | 3.272346327

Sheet: Wing
Design Parameters |  |  |  | Airfoil Data |  |  | Air Properties
M | 0.04 |  |  | Name | NACA 23012 |  | Cruise Alt. (ft) | 1000 | ft
S | 4.354978219 | ft2 |  | Clmax | 1.3 |  | V | 44.02 | f/s
A | 7.0 |  |  | Cla | 0.1 | 1/deg | r | 0.0744742049 | lbm/f^3
LLE | 0 | deg |  | a.c. | 0.253 | c | q | 2.241294924 | lbf/f^2
t/c | 0.12 |  |  | a0L | -1.5 | deg | m | 1.07e-05 | lbm/(f-s)
l | 1.00 |  |  | Cd0 | 0.01 |  | n (cruise) | 0.0001436739072 | f^2/s
W c-start | 3.545557854 | lbf/f^2 |  | rle | 0.0024 | c
W c-end | 3.545557854 | lbf/f^2 |  | ClminD | 0.1 - 0.4
q c-start | 2.24 | lbf/f^2 |  | (t/c)max | 0.12 | c
q c-end | 2.24 | lbf/f^2
Cl c-start | 0.36
Cl c-end | 0.36
Calculations |  |  |  | Sweep Angles
b | 5.5 | ft |  |  | x/c | Lx/c (deg)
Meff | 0.04 |  |  | LE | 0.00 | 0.0
cr | 0.8 | ft |  | 1/4C | 0.25 | 0.0
ct | 0.8 | ft |  | a.c | 0.25 | 0.0
m.a.c. | 0.8 | ft |  | (t/c)max | 0.12 | 0.0
 |  |  |  | TE | 1.00 | 0.0
b | 1.00
CLa | 0.083 | 1/deg |  | Viscous Drag
CLo | 0.12 |  |  | V_eff | 44.024 | f/s
atrim | 2.9 | deg |  | q_eff | 2.241294924 | lbf/f^2
CLtrim | 0.363 |  |  | Re_mac | 241688.2689
k | 0.0568410511 |  |  | sqrt(Re) | 491.6180111
CD | 0.014 |  |  | Cf | 0.002701284269
L/D | 25.58 |  |  | S_wet | 8.881542579 | ft2
 |  |  |  | F | 1.216712236
 |  |  |  | Q | 1
Total Drag | 0.138631207 | lbf |  | CD0 | 0.006702866661
Plotting:
Spanwise View
x | y
0 | 0
0.8 | 0
0.7887583569 | 2.760654249
0 | 2.760654249
0 | 0
Lift Curves
a | Cl | a | CL
-1.5 | 0 | -1.5 | 0
11.5 | 1.3 | 11.5 | 1.075963809

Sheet: Fuse
 |  |  | Fuselage Design
Flight Regime Data:
Cruise Mach | 0.04
Cruise Alt. (ft) | 1000
V (f/s) | 44.02
r (lbm/f^3) | 0.0744742049
q (lbf/f^2) | 2.241294924
m (lbm/(f-s)) | 1.07e-05
n (cruise) (f^2/s) | 0.0001436739072
Dimension Data: |  |  | Form Factors:
D-max (ft) | 0.333 |  | F | 1.104804527
L/D | 9 |  | Q | 1
L (ft) | 3.00 |  | F*Q | 1.104804527
S (f^2) | 4.354978219
Viscous Drag Calculations: |  |  | Cone-Cylinder
x/L | x (ft) | x-L/4 (ft) | D (ft) | P (ft) | Sw(ft^2) | Rex | CF | Drag (lbf)
0.00 | 0.00 | -0.75 | 0 | 0.0
0.10 | 0.30 | -0.45 | 0.333 | 1.0 | 0.3 | 91832.90871 | 0.00438226771 | 0.003402234205
0.20 | 0.60 | -0.15 | 0.333 | 1.0 | 0.3 | 183665.8174 | 0.003098731215 | 0.002405742878
0.30 | 0.90 | 0.15 | 0.05 | 0.2 | 0.04707676591 | 275498.7261 | 0.002530103442 | 0.0002949370622
0.40 | 1.20 | 0.45 | 0.05 | 0.2 | 0.04707676591 | 367331.6349 | 0.002191133855 | 0.0002554229884
0.50 | 1.50 | 0.75 | 0.05 | 0.2 | 0.04707676591 | 459164.5436 | 0.001959809699 | 0.000228457266
0.60 | 1.80 | - | 0.05 | 0.2 | 0.04707676591 | 550997.4523 | 0.001789053301 | 0.0002085519967
0.70 | 2.10 | - | 0.05 | 0.2 | 0.04707676591 | 642830.361 | 0.001656341506 | 0.0001930816304
0.80 | 2.40 | - | 0.05 | 0.2 | 0.04707676591 | 734663.2697 | 0.001549365607 | 0.0001806113272
0.90 | 2.70 | - | 0.05 | 0.2 | 0.04707676591 | 826496.1784 | 0.001460755903 | 0.0001702819923
1 | 3.00 | - | 0 | 0.0 | 0.0 | 918329.0871 | 0.001385794728 | 0
Totals: |  |  |  |  | 1.0 |  |  | 0.00734
Total Drag: | 0.00734
(lbf)
Equiv. CD | 0.0007519187395

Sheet: Tail
Main Wing Reference |  |  |  | Air Properties
b | 5.5 | ft | Cruise Alt. (ft) | 1000 | ft
m.a.c. | 0.8 | ft | V | 44.02 | f/s
S | 4.354978219 | ft2 | r | 0.0744742049 | lbm/f^3
M | 0.04 |  | q | 2.241294924 | lbf/f^2
LLE | 0 | deg | m | 1.07e-05 | lbm/(f-s)
t/c | 0.12 |  | n (cruise) | 0.0001436739072 | f^2/s
l | 1.00
Vertical Tail
Design Parameters |  |  | Airfoil Data
Cvt | 0.04 |  | Name | NACA 0009
Lvt | 2.6 | ft | Clmax | 1.1
LLE | 0 | deg | Cla | 0.111 | 1/deg
t/c | 0.09 |  | a.c. | 0.25 | c
l | 1.00 |  | a0L | 0 | deg
Avt | 1.50 |  | Cd | 0.01
Calculations |  |  | Sweep Angles |  |  | Viscous Drag
Svt | 0.3699 | ft2 |  | x/c | Lx/c (deg) | V_eff | 44.024 | f/s
b | 0.7 | ft | LE | 0.00 | 0.0 | q_eff | 2.241294924 | lbf/f^2
cr | 0.5 | ft | 1/4 chord | 0.25 | 0.0 | M_eff | 0.04
ct | 0.5 | ft | (t/c)max | 0.35 | 0.0 | Re_mac | 152167.9851
m.a.c. | 0.5 | ft | TE | 1.00 | 0.0 | sqrt(Re) | 390.0871506
b | 1.00 |  |  |  |  | Cf | 0.003404367454
CLa | 0.037 | 1/deg |  |  |  | S_wet | 0.7486558729 | ft2
 |  |  |  |  |  | F | 0.958612656
 |  |  |  |  |  | Q | 1.05
Total Drag | 0.006 | lbf |  |  |  | CD0 | 0.006934840536
Spanwise View
x | y
0 | 0
0.5 | 0
0.4966056915 | 0.7
0 | 0.7
0 | 0
Horizontal Tail
Design Parameters |  |  | Airfoil Data
Cht | 0.50 |  | Name | NACA 64-004
Lht | 2.6 | ft | Clmax | 0.8
LLE | 0 | deg | Cla | 0.111 | 1/deg
t/c | 0.09 |  | a.c. | 0.258 | c
l | 1.00 |  | a0L | 0 | deg
Aht | 5.00 |  | Cd | 0.004
Calculations |  |  | Sweep Angles |  |  | Viscous Drag
Sht | 0.66058182 | ft2 |  | x/c | Lx/c (deg) | V_eff | 44.024 | f/s
b | 1.8 | ft | LE | 0.00 | 0.0 | q_eff | 2.241294924 | lbf/f^2
cr | 0.4 | ft | 1/4 chord | 0.25 | 0.0 | M_eff | 0.04
ct | 0.4 | ft | (t/c)max | 0.35 | 0.0 | Re_mac | 111375.5608
m.a.c. | 0.4 | ft | TE | 1.00 | 0.0 | sqrt(Re) | 333.7297721
b | 1.00 |  |  |  |  | Cf | 0.003979267392
CLa | 0.074 | 1/deg |  |  |  | S_wet | 1.336885487 | ft2
 |  |  |  |  |  | F | 0.958612656
 |  |  |  |  |  | Q | 1.05
Total Drag | 0.012 | lbf |  |  |  | CD0 | 0.008105936032
Spanwise View
x | y
0 | 0
0.4 | 0
0.3634781479 | 0.9
0 | 0.9
0 | 0

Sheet: TO_L
Take-Off
CD_0 | 0.015 | mu_TO | 0.05
A | 7 | T_max (lb) | #REF!
H (f) | 0 | f_LG | 0.1949351769
CL_G | 2 | A_LG (f^2) | 1
W_TO (lb) | 3.64229727 | deltCD_0_flap | 0.05
S (f^2) | 4.354978219 | gamma_CL (deg) | 3
 |  | H_obstacle (f) | 10
k | 0.05684109912 | T/W | #REF!
rho (lbm/f^3) | 0.076474 | f1 (f/s^2) | #REF!
W/S (lb/f^2) | 0.8363525802 | deltCD_0_LG | 0.04476145852
S (f^2) | 4.354978219 | f2 (f^-1) | -0.0056436861
V_T-O (f/s) | 22.51888998 | R_TR (f) | 104.9897321
q_T_O (lb/f^2) | 0.6021738577 | H_TR (f) | 0.1438845359
 |  | S_G (f) | #REF!
 |  | S_R (f) | 67.55666994
 |  | S_TR (f) | 5.494733386
 |  | S_CL (f) | 188.0660455
 |  | S_T-O (f) | #REF!
Landing
W_L (lb) | 3.456918908 | D_50 (lb) | 0.9847765864
W/S (lb/f^2) | 0.7937855793 | gamma_A (deg) | -16.55116284
V_50 (f/s) | 23.76654146 | gamma_A _act | -3
V_TD (f/s) | 21.02424821 | R_TR (f) | 82.65060178
q_50 (lb/f^2) | 0.6707488145 | H_TR (f) | 0.1132630976
q_TD (lb/f^2) | 0.5248907143 | f1 (f/s^2) | 8.623958934
mu _L | 0.6 | f2 (f^-1) | 0.0470411526
T_L (lb) | 3
 |  | S_A (f) | 951.8964512
 |  | S_TR (f) | 4.325594628
 |  | S_FR (f) | 63.07274464
 |  | S_B (f) | -13.04209052
 |  | S_L (f) | 1006.2527
 |  | 1.6(S_L) (f) | 1610.00432
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

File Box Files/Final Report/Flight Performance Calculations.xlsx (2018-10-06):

Trial | Climb Time (ms) | Climb Height (ft) | Glide Time (ms) | Glide Height (ft) | Rate (ft/min)
Climb 1 Bottom | 336500.000 | 172.000
Climb 1 - End of Constant Climb | 344200.000 | 332.000
Climb 1 - Top | 351200.000 | 396.000
First Half | 0.128 | 160.000 |  |  | 1246.753247
Second Half | 0.117 | 64.000 |  |  | 548.5714286
Total | 0.245 | 224.000 |  |  | 914.2857143
Glide 1 - Top |  |  | 351000.000 | 396.000
Glide 1 - End of Steep Glide |  |  | 357100.000 | 350.000
Glide 1 - End of Glide |  |  | 375000.000 | 172.000
First Half |  |  | 0.102 | -46.000 | -452.4590164
Second Half |  |  | 0.298 | -178.000 | -596.6480447
Total |  |  | 0.400 | -224.000 | -560
Climb 2 - Bottom | 415500.000 | 134.000
Climb 2 - Top | 428100.000 | 339.000
Total | 0.210 | 205.000 |  |  | 976.1904762
Glide 2 - Top |  |  | 428100.000 | 339.000
Glide 2 - End of Constant Glide |  |  | 439400.000 | 238.000
Glide 2 - End of Glide |  |  | 454800.000 | 134.000
First Half |  |  | 0.1883333333 | -101.000 | -536.2831858
Second Half |  |  | 0.2566666667 | -104.000 | -405.1948052
Total |  |  | 0.445 | -205.000 | -460.6741573
Success Factor
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

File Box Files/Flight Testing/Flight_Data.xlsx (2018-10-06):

Milliseconds | Altitude | Speed | ThermoA*10 | ThermoB*10 | GPSLat | GPSLon | GPSAlt | GPSSpeed | GPSCourse | GPSDist | GPSUTC
0 | 0 | 0 | 320 | 320 | 41.51959333 | -86.23998167 | 938.3 | 0.8 | 19.1 | 0 | 58107000
100 | 0 | 0 | 320 | 320 | 41.51959333 | -86.23998167 | 938.3 | 0.8 | 19.1 | 0 | 58107000 | Data | Value
200 | 0 | 0 | 320 | 320 | 41.51959333 | -86.23998167 | 938.3 | 0.8 | 19.1 | 0 | 58107000 | Avg. Flight Speed | 34.1646 | mph
300 | 0 | 0 | 320 | 320 | 41.51959333 | -86.23998167 | 938.3 | 0.8 | 19.1 | 0 | 58107000 | Max Flight Speed | 52.8 | mph
400 | 0 | 0 | 320 | 320 | 41.51959333 | -86.23998167 | 938.3 | 0.8 | 36.7 | 0 | 58109100 | Min Flight Speed | 20 | mph
500 | 0 | 0 | 320 | 320 | 41.51959333 | -86.23998167 | 938.3 | 0.8 | 36.7 | 0 | 58109100 | Max Climb Rate | 22.62 | ft/s
600 | 0 | 0 | 320 | 320 | 41.51959 | -86.23998667 | 938.3 | 0.7 | 38.9 | 1.8 | 58109200 | Min Glide Rate | -7.66 | ft/s
700 | 0 | 0 | 320 | 320 | 41.51961667 | -86.24 | 941.6 | 0.6 | 40.5 | 9.9 | 58109600 | Max Sustained Turn Rate
800 | 0 | 0 | 320 | 320 | 41.51961667 | -86.24 | 941.6 | 0.6 | 40.5 | 9.9 | 58109600 | Average Glide Rate | -8.59 | ft/s
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
